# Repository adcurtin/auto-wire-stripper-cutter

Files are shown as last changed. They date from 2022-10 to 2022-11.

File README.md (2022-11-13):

# remix

this is my remix of [ProjectswithRed](https://www.youtube.com/c/ProjectswithRed)'s automatic wire stripper. I've recreated (almost) all of the 3d models with openscad, to allow for parameter tweaking. I switched the extruder to an openscad model, and tweaked that extensively as well.

# Automatic Wire Stripper and Cutter

A 3D printed automatic wire stripper and cutter. I had some old 3d printers that had been retired, I reused those parts for this project. I used a mainboard from a wanhao i3, and 24v steppers from a makerbot replicator 1 (though the wanhao steppers would've been fine at 12v). I'm using a 20V 65W lenovo laptop power supply that had a frayed end.

I'm running Marlin on this, since that can already do everything I need and I don't have to write or maintain any code :).

# Marlin notes

X and Y endstops are always triggered, so `G28` won't fail.
I modified the Z endstop to be optical, so that's inverted from the wanhao's config.

# Components

- I used some parts from old, dead 3d printers. mainboard, lcd, and rotary encode from a wanhao i3, steppers from a makerbot replicator 1, and a power supply from a lenovo laptop that had the end frayed / broken.

- [D8mm L100mm lead screw](https://www.amazon.co.uk/dp/B07QWKG317?ref_=cm_sw_r_cp_ud_dp_JMAC4EKE28W5Z3GSZSN8) (x2), for the linear motion.
- [D8mm lead screw nut](https://www.amazon.co.uk/dp/B07QWKG317?ref_=cm_sw_r_cp_ud_dp_JMAC4EKE28W5Z3GSZSN8) (x2), to attach the top blade housing to the lead screws.
- [5x8mm rigid shaft coupler](https://www.amazon.co.uk/dp/B096G1GZH5?ref_=cm_sw_r_cp_ud_dp_VWE1T2SQZQB0X13TQ1F7) (x2), to attach the lead screws to the stepper motors.
- [10mm magnets](https://www.amazon.co.uk/dp/B08FSTRRDR?ref_=cm_sw_r_cp_ud_dp_13WEC590XVADQKN2RJ0W) (x2), to attach the container.
- [KNIPEX V-blades](https://www.amazon.co.uk/dp/B00161GBDW?ref_=cm_sw_r_cp_ud_dp_S63KK1ZZ8DPRHWMBEFJC), to cut and strip the wires.

# 3D printing

Please refer to the `/3d_printing` directory.

# Assembly layout
This is the layout of the components on the board. Use this only for reference on roughly where you should fix the components to the board. I don't suggest using this for exact measurements as you should position the components where it is appropriate for your version of the project.

[Layout PDF](./assembly_layout.pdf).

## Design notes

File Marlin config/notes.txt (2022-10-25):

extruder axis - connected to original y axis - swap with E0 axis pin definition? just use e0 axis
extruder axis steps per mm - 

z axis - connected to original z axis
z axis endstop - minimum, connected to z endstop

z axis endstop sets minimum, allow jog 1mm past?
live adjust z? use this to adjust z home to be spot for stripping? or cut spot? or don't use?

z axis steps per mm - ?

lcd for melzi

shorter machine name - done

invert x and y endstops, so they're always homed, to fix homing - or just disable the endstops? and disable homing direction - done

todo:

allow Z to move past endstop a little? - how? MANUAL_[XYZ]_HOME_POS - try more - 1.6 good
longer z axis - try 90mm? try 110 then dial it back , trying 140… 135 good

check out babystepping? for live adjust z           

calibrate steps per mm on extruder          
    etrudeded 100mm, got 105mm. changed to 95mm   

more extruder speed
    try with gcode hooked up to computer
    increased manual feedrate

test running gcode from SD

NTH:

custom menu (menus?)
    check out extensible UI?

different home / status screen - custom status bitmap

bootscreen

custom predefined gcode for different lengths / wire sizes

disable x and y axes?
    no can do

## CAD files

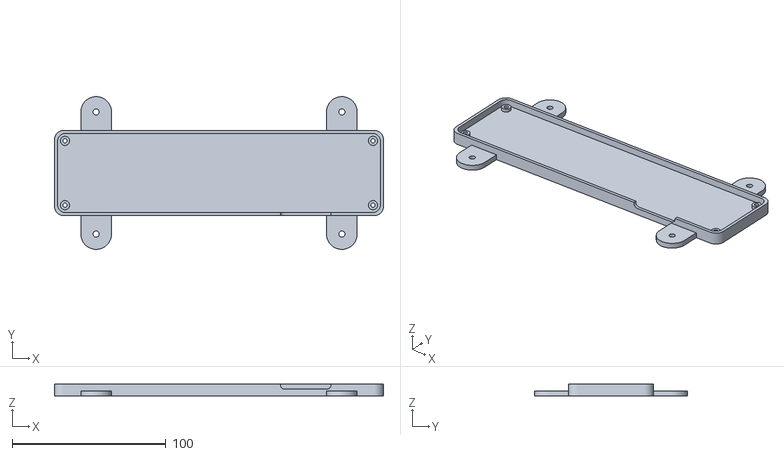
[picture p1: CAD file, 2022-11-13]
3d_printing/mainboard/mainboard case.stl
214.3 x 99.5 x 8.00

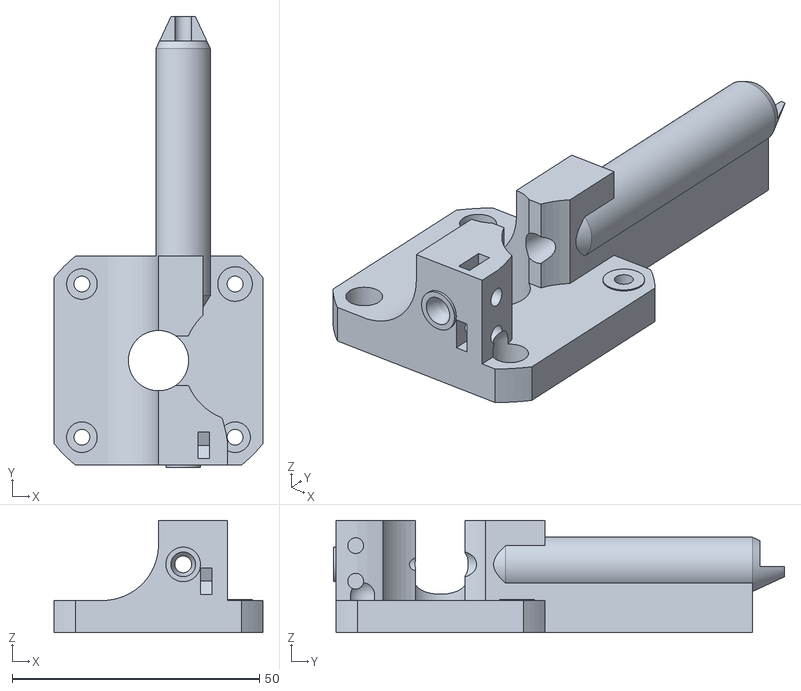
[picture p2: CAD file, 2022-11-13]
3d_printing/extruder/compact_extruder_mount motor.stl
42.3 x 91.3 x 22.7

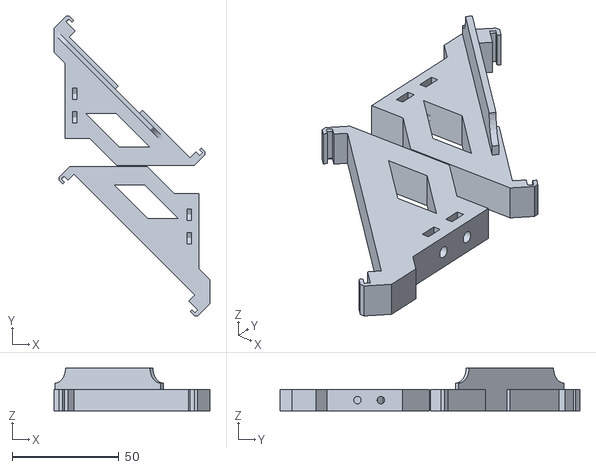
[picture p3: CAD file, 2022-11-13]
3d_printing/lcd/lcd_supports.stl
72.9 x 140.6 x 20.0

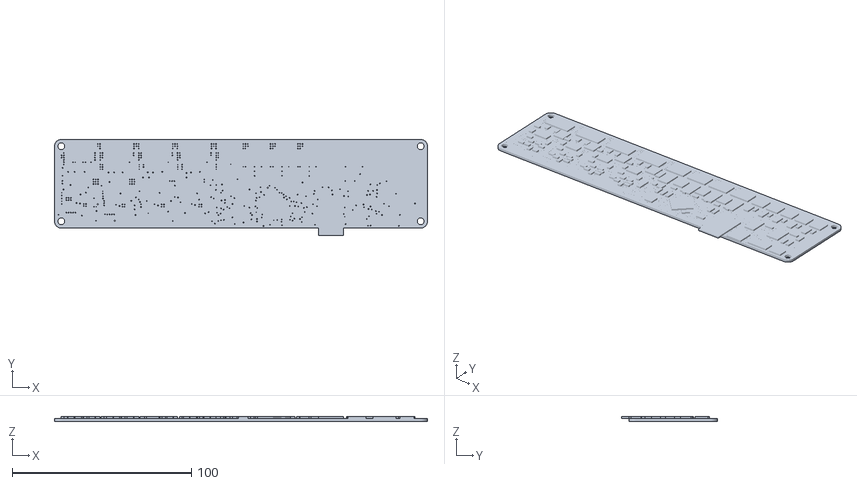
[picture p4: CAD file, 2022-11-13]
3d_printing/mainboard/melzi_pcb.stl
208.3 x 53.7 x 2.60

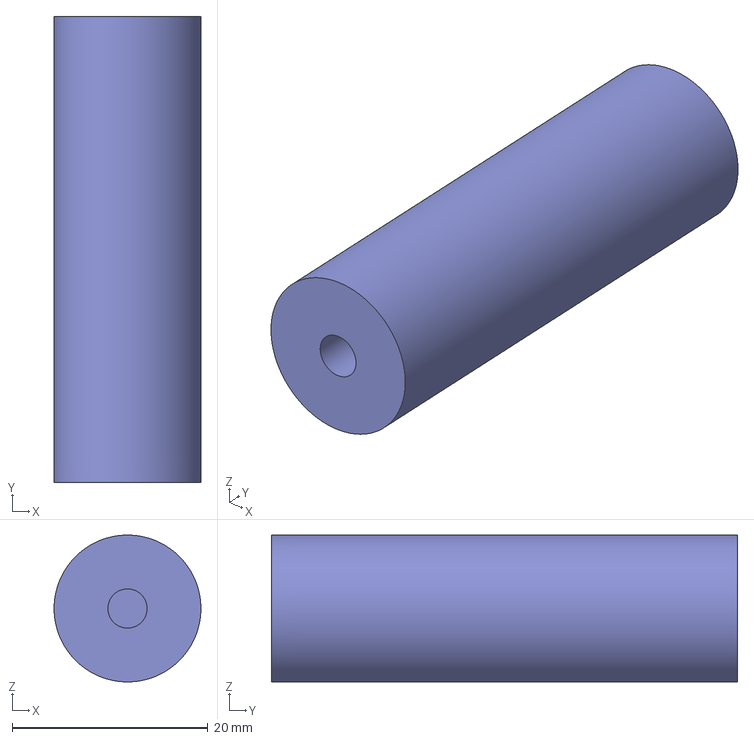
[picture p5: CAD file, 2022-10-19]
3d_printing/original models/spoolHolder_cylinder.3mf
15.0 x 47.6 x 15.0 mm

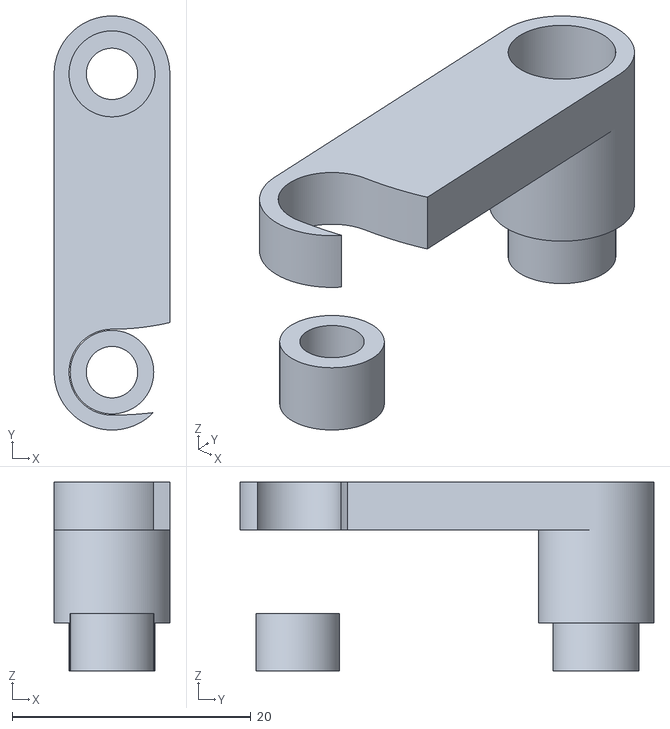
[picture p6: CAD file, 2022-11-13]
3d_printing/wire straightener/wire guide.stl
9.70 x 34.7 x 15.8

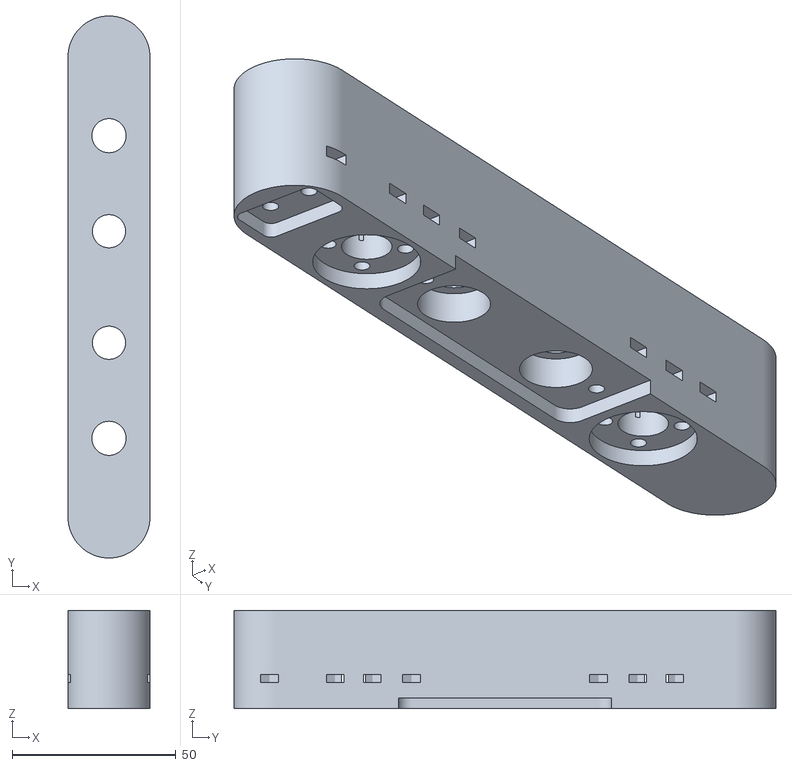
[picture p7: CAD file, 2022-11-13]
3d_printing/z axis attachment.stl
25.0 x 165.3 x 30.0

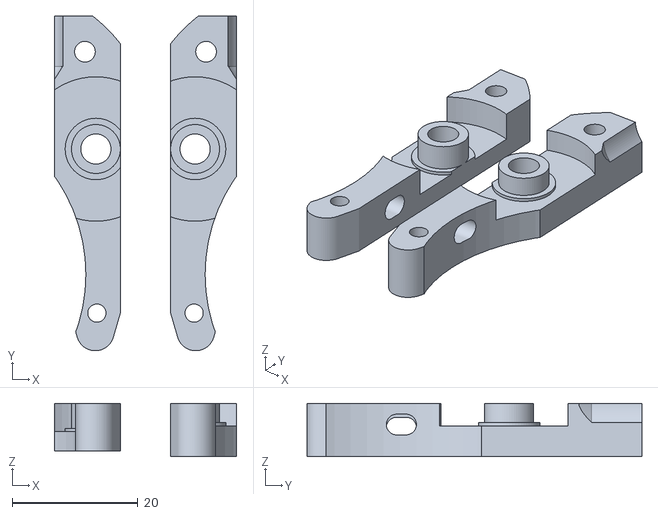
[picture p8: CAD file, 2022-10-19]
3d_printing/extruder/compact_extruder_mount idler.stl
29.0 x 53.3 x 8.45

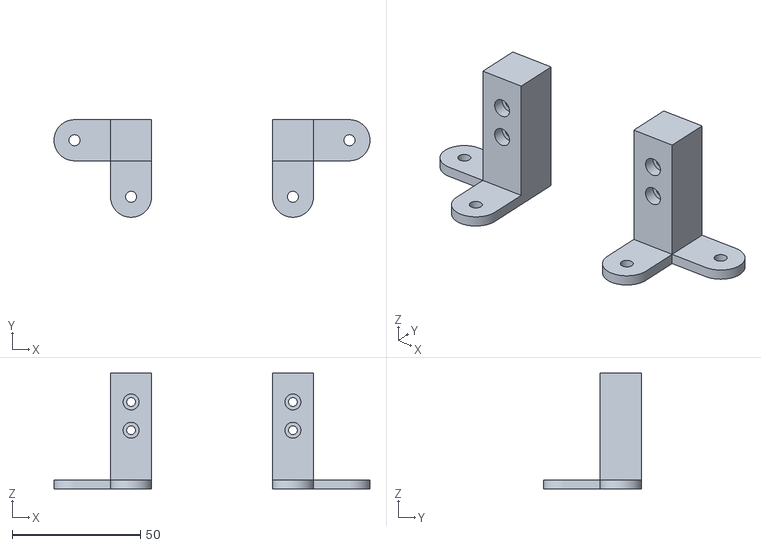
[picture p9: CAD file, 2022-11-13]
3d_printing/lcd mount.stl
123.0 x 38.0 x 45.0

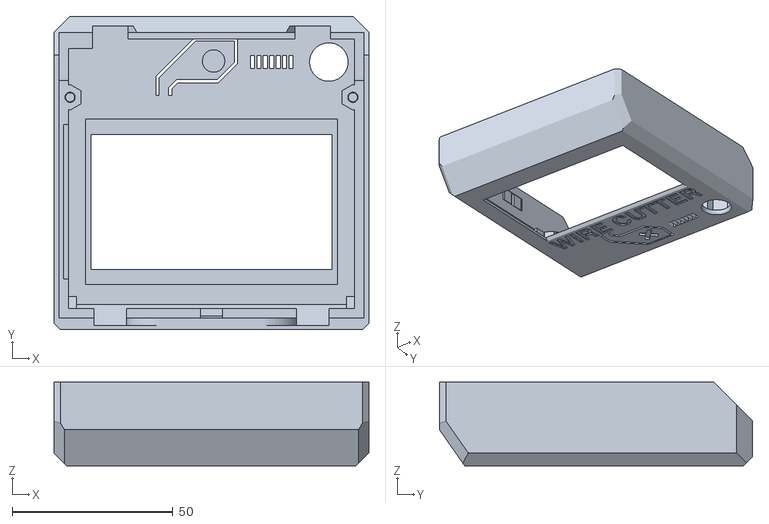
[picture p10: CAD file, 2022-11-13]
3d_printing/lcd/lcd_cover.stl
98.0 x 97.5 x 26.0

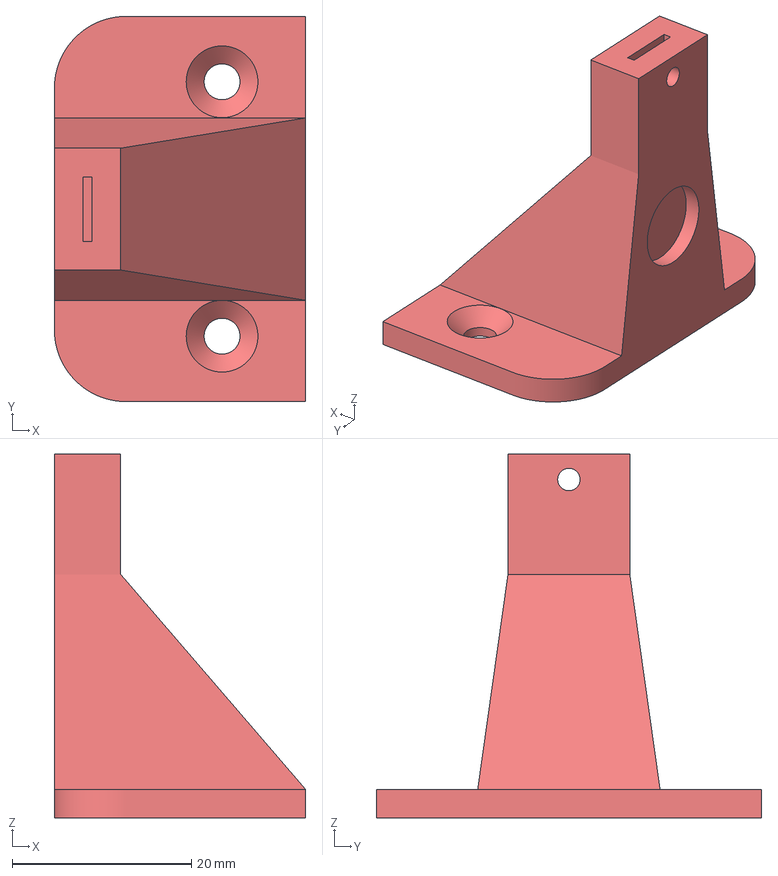
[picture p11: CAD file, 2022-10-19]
3d_printing/original models/bottomBlade_housing.3mf
28.0 x 43.0 x 40.6 mm

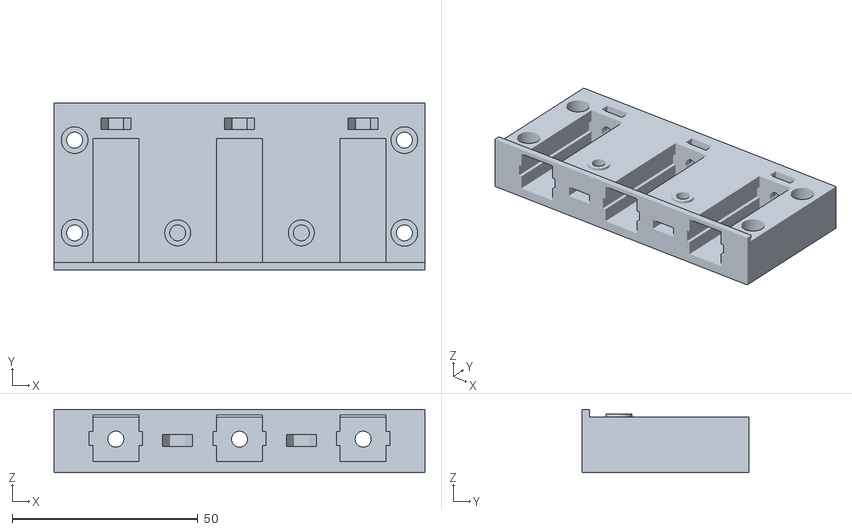
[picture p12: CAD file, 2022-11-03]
3d_printing/wire straightener/wire straightener.stl
100.0 x 45.0 x 17.0

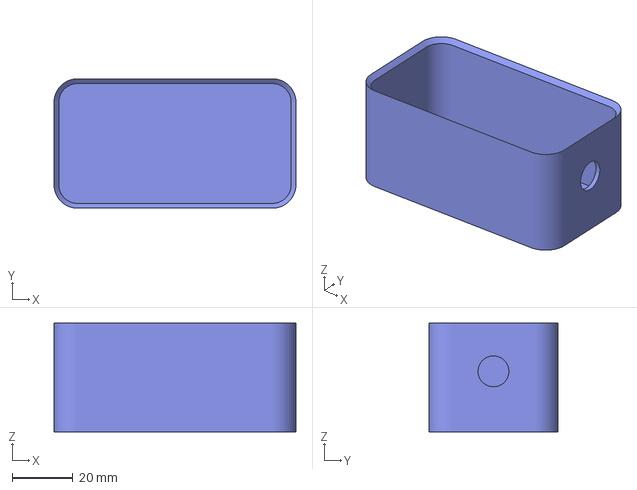
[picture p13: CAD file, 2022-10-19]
3d_printing/original models/container.3mf
80.0 x 42.8 x 36.0 mm

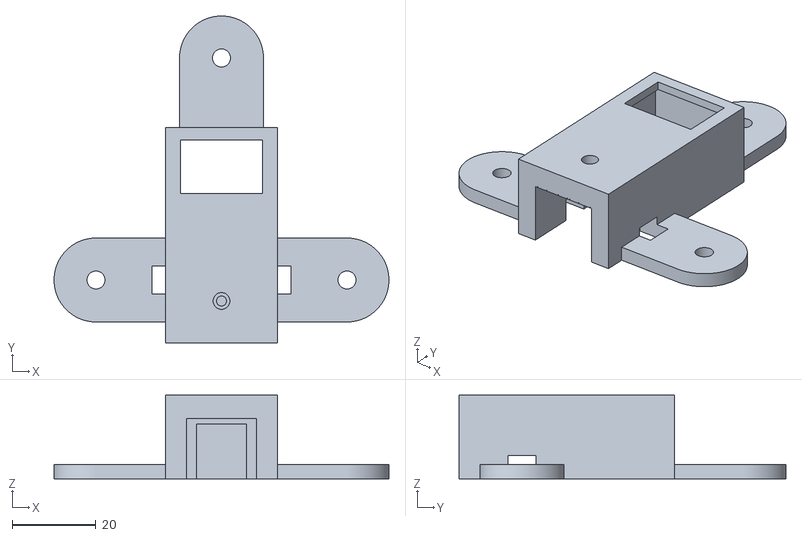
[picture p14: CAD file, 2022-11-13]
3d_printing/power module.stl
79.8 x 77.9 x 20.0

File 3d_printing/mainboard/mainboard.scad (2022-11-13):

include <OpenSCAD-common.scad>
use <melzi.scad>

// Melzi Dimensions approx 210mm x 50mm x 17mm
melzi_dimensions = [208.3, 49.55, 1.7];
melzi_hole_offset = [3.81, 3.81, 0];


$fn=50;


base_th = 3.5;

th=2;
case_clearance = 1;


case_w = melzi_dimensions[1] + 2*th + 2*case_clearance;
case_l = melzi_dimensions[0] + 2*th + 2*case_clearance;

case_h  = 8;

mount_tab_w = 20;

mount_tab_l = 35;

mount_tab_gap = 160;

mount_tab_r = 10;



// melzi_holes();/
translate([0,0,base_th + 2]) %melzi_pcb();


module mainboard_case(cutout=0){

    if(cutout==0) {
    difference() {
        translate([-case_l/2, -case_w/2, 0]) roundedRect([case_l, case_w, case_h],6);
        translate([-melzi_dimensions[0]/2 - case_clearance, -melzi_dimensions[1]/2 - case_clearance, base_th]) roundedRect([melzi_dimensions[0]+2*case_clearance, melzi_dimensions[1]+2*case_clearance, case_h],4+case_clearance);
        melzi_holes() cylinder(h=30, d=2.8, center = true);

        translate([40, -melzi_dimensions[1]/2, base_th + 1])  rotate([90, 0, 0]) roundedRect([20+13,10,10],3);
        // #translate([-100, melzi_dimensions[1]/2, th + 42])  rotate([-90, 0, 0]) roundedRect([200,40,10],7);
    }
    melzi_holes() difference() {
        cylinder(h=base_th+2, d=6);
        cylinder(h=30, d=2.8, center = true);
    }

    translate([0, 0, 0]) difference() {
        union() {
            translate([-mount_tab_w/2 + mount_tab_gap/2,  melzi_dimensions[1]/2 - mount_tab_r, 0])  roundedRect([mount_tab_w, mount_tab_l, 3.5], mount_tab_r);
            translate([-mount_tab_w/2 - mount_tab_gap/2,  melzi_dimensions[1]/2 - mount_tab_r, 0])  roundedRect([mount_tab_w, mount_tab_l, 3.5], mount_tab_r);
            translate([-mount_tab_w/2 + mount_tab_gap/2, -melzi_dimensions[1]/2 - mount_tab_l + mount_tab_r, 0])  roundedRect([mount_tab_w, mount_tab_l, 3.5], mount_tab_r);
            translate([-mount_tab_w/2 - mount_tab_gap/2, -melzi_dimensions[1]/2 - mount_tab_l + mount_tab_r, 0])  roundedRect([mount_tab_w, mount_tab_l, 3.5], mount_tab_r);
        }
        translate([ mount_tab_gap/2,  melzi_dimensions[1]/2 - 2*mount_tab_r + mount_tab_l, -1]) cylinder(h=10, d=4);
        translate([-mount_tab_gap/2,  melzi_dimensions[1]/2 - 2*mount_tab_r + mount_tab_l, -1]) cylinder(h=10, d=4);
        translate([ mount_tab_gap/2, -melzi_dimensions[1]/2 + 2*mount_tab_r - mount_tab_l, -1]) cylinder(h=10, d=4);
        translate([-mount_tab_gap/2, -melzi_dimensions[1]/2 + 2*mount_tab_r - mount_tab_l, -1]) cylinder(h=10, d=4);
    }
    }

    if(cutout) {
        translate([ mount_tab_gap/2,  melzi_dimensions[1]/2 - 2*mount_tab_r + mount_tab_l, -1]) children();
        translate([-mount_tab_gap/2,  melzi_dimensions[1]/2 - 2*mount_tab_r + mount_tab_l, -1]) children();
        translate([ mount_tab_gap/2, -melzi_dimensions[1]/2 + 2*mount_tab_r - mount_tab_l, -1]) children();
        translate([-mount_tab_gap/2, -melzi_dimensions[1]/2 + 2*mount_tab_r - mount_tab_l, -1]) children();
    
    }


}


mainboard_case(0) cylinder(h=10, d=2);

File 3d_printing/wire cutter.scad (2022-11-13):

include <OpenSCAD-common.scad>
use <extruder/compact_extruder_mount.scad>
use <wire straightener/wire straightener.scad>
use <lcd/lcd.scad>
use <mainboard/mainboard.scad>



fast_preview = 0;

module fp(){
    if(fast_preview) render() children();
    else children();
}

//animation
anim = 2*($t < 0.5 ? $t : (1-$t));

anim_height = 20*anim;

// echo(anim_height);

$fn=150;


ep = 0.01 * 1;


spool_bearing_d = 16;
spool_bearing_th = 4.9;
spool_bearing_screwhead_d = 12;
spool_bearing_screwhead_th = 3;
spool_cylinder_th = 2;
spool_cylinder_d = 18.5;
spool_h     = 48;
spool_d     = 130;


corner_rad = 7;

spool_base_x  = 40;
spool_base_y  = 53;
spool_base_th = 3.5;
spool_side_th = 4.8;


container_h = 36;
container_l = 120;
container_w = 42.8;
container_th = 2;
container_radius = 8;

container_small_l = 16;




motor_mount_th = 3.65;

nema_w = 42.3;
nema_h = 36;
nema_screw_w = 31;
nema_bushing_h = motor_mount_th;
nema_bushing_d = 23;

z_axis_stop_height = 47.5;


mech_endstop_w = 5.75;
mech_endstop_l = 12.6;
mech_endstop_h = 6.5;
mech_endstop_screw_d = 1.9;
mech_endstop_screw_gap = 6.65;
mech_endstop_screw_z_o = 1.5;


mech_endstop_e_h = 2.5; //extra height above the switch
mech_endstop_z_o =  z_axis_stop_height - mech_endstop_h - mech_endstop_e_h;//33.5 + 5;


//slop in the leadscrews, endstop springs to help

mech_endstop_spring_od = 5.3; //outside diameter for clearance
mech_endstop_spring_id = 3.4;
mech_endstop_spring_l = 25;
mech_endstop_spring_c_l = 10;

mech_endstop_spring_e_d = 5.1; //end diameter to hold the springs
mech_endstop_spring_e_l = 4;



optical_endstop_z_o = z_axis_stop_height - 8;




z_flag_base_th  = 3.25;
z_flag_base_w   = 20;
z_flag_base_l   = 12;

z_flag_base_o   = 19.65;



z_flag_w        = 2;
z_flag_l        = 8;
z_flag_h        = 10;


//z axis attachment
attachment_h = 30;
attachment_w = 25;
attachment_screw_l = 14;
attachment_nut_dp = 8;
attachment_nut_rotation = 30;

threaded_rod_d = 10.4;
blade_stepper_gap = 92.265;





//blade holder
top_blade_holder_w = 65;
top_blade_holder_r = 4;
top_blade_holder_l = 22;
top_blade_holder_h = 3.25;
top_blade_holder_screw_gap = 57;


bottom_blade_holder_w = 43;
bottom_blade_holder_r = 8;
bottom_blade_holder_l = 24.8 + 3.4;
bottom_blade_holder_h = 3.25;
bottom_blade_holder_screw_gap = 28.5;
bottom_blade_holder_screw_x = 15.4;


blade_holder_w  = 13.6;
blade_holder_l  = 8;
blade_holder_h  = 15 + .8;

//blades
blade_w = 7;
blade_th = 1;
top_blade_h = 11.25;
bottom_blade_h = 13.15;
bottom_blade_e_w = 11;
bottom_blade_e_w_h = 3.75;
bottom_blade_e_w_h_o = 2.8;

blade_cut = 3.3;
blade_notch_w = 2.5;
blade_notch_o = top_blade_h - 4.6;

blade_y_offset = 49 + blade_cut;
blade_overcut = 1;

blade_overlap = .1;
blade_over_angle = 4;


blade_holder_screw_d = 2.4;
screwhole_d = 3.3;
base_screwhole_d = 4.3;



linear_rod_d = 8.1;
linear_rod_l = 175;
linear_rod_gap = 34;

linear_bearing_d = 15;
linear_bearing_l = 17;

linear_slider_d = 15;
linear_slider_l = 40;

linear_slider_base_th = 5.3;
linear_slider_base_d = 32;
linear_slider_base_w = 21;

// linear_slider_screwhead_d = 5.6;
linear_slider_screw_d = screwhole_d;
linear_slider_screw_gap = 23.75;

linear_slider_nut_dp = 10;



mounting_board_w = 300;
mounting_board_l = 500;
mounting_board_th = 18;



module linear_slider(cutout=0) {
    difference() {
        union() {
            intersection() {
                cylinder(h=linear_slider_base_th, d=linear_slider_base_d);
                translate([-linear_slider_base_d/2, -linear_slider_base_w/2, 0]) cube([linear_slider_base_d, linear_slider_base_w, linear_slider_base_th]);
            }
            cylinder(h=linear_slider_base_th + linear_slider_l, d=linear_slider_d);
        }
        if(cutout==0) translate([0, 0, -1]) linear_rod();

        translate([linear_slider_screw_gap/2, 0, -1]) cylinder(h=linear_slider_base_th + 2, d=linear_slider_screw_d);
        translate([-linear_slider_screw_gap/2, 0, -1]) cylinder(h=linear_slider_base_th + 2, d=linear_slider_screw_d);

    }

    if(cutout) {
        translate([linear_slider_screw_gap/2, 0, -1]) cylinder(h=linear_slider_base_th + linear_slider_nut_dp + 0.5, d=linear_slider_screw_d);
        translate([-linear_slider_screw_gap/2, 0, -1]) cylinder(h=linear_slider_base_th + linear_slider_nut_dp + 0.5, d=linear_slider_screw_d);

        // nut slots
        hull() {
            translate([linear_slider_screw_gap/2, 0, linear_slider_nut_dp]) M3_hex_nut();
            translate([linear_slider_screw_gap, 0, linear_slider_nut_dp]) M3_hex_nut();
        }

        hull() {
            translate([-linear_slider_screw_gap/2, 0, linear_slider_nut_dp]) M3_hex_nut();
            translate([-linear_slider_screw_gap, 0, linear_slider_nut_dp]) M3_hex_nut();
        }
    }
}

// !linear_slider(1);


module linear_bearing() {
    difference() {
        cylinder(h=linear_bearing_l, d=linear_bearing_d);
        translate([0, 0, -1]) linear_rod();
    }
}


module linear_rod(extra_d=0) {
    cylinder(h=linear_rod_l, d=linear_rod_d + extra_d);
}



// top_blade();

module top_blade(cutout=0){
    translate([0, 0, blade_y_offset-blade_cut]) {
        if(cutout) translate([-10, 0, blade_notch_o + blade_notch_w/2]) rotate([0, 90, 0]) cylinder(h=blade_th+20, d=blade_notch_w);
        translate([0, 0, blade_cut]) rotate([0, blade_over_angle, 0]) translate([0, 0, -blade_cut]) 
        difference() {
            union() {
                translate([-blade_th, -blade_w/2, 0]) cube([blade_th, blade_w, top_blade_h]);
            }
            if(cutout==0) hull() {
                translate([-10, 0, blade_notch_o + blade_notch_w/2]) rotate([0, 90, 0]) cylinder(h=blade_th+20, d=blade_notch_w);
                translate([-1, 0, top_blade_h + blade_notch_o]) rotate([0, 90, 0]) cylinder(h=blade_th+2, d=blade_notch_w);
            }

            if(cutout==0)
            translate([0, 0, blade_cut]) 
            scale([1, 1, 1.4]) 
            rotate([180+45, 40, 0]) 
            translate([-3, 0, 0]) cube([blade_cut+4, blade_cut+1, blade_cut+1]);
        }
    }
}

module bottom_blade(cutout=0){
    translate([-blade_overlap, 0, blade_y_offset + blade_cut + blade_overcut]) rotate([0, 180, 0]) {
        if(cutout) translate([-10, 0, blade_notch_o + blade_notch_w/2]) rotate([0, 90, 0]) cylinder(h=blade_th+20, d=blade_notch_w);
        translate([0, 0, blade_cut]) rotate([0, blade_over_angle, 0]) translate([0, 0, -blade_cut])  difference() {
            union() {
                translate([-blade_th, -blade_w/2, 0]) cube([blade_th, blade_w, bottom_blade_h]);
                translate([-blade_th, -bottom_blade_e_w/2, bottom_blade_e_w_h_o]) cube([blade_th, bottom_blade_e_w, bottom_blade_e_w_h]);
            }
            if(cutout==0) hull() {
                translate([-10, 0, blade_notch_o + blade_notch_w/2]) rotate([0, 90, 0]) cylinder(h=blade_th+20, d=blade_notch_w);
                translate([-1, 0, top_blade_h + blade_notch_o]) rotate([0, 90, 0]) cylinder(h=blade_th+2, d=blade_notch_w);
            }

            if(cutout==0)
            translate([0, 0, blade_cut]) 
            scale([1, 1, 1.4]) 
            rotate([180+45, 40, 0]) 
            translate([-3, 0, 0]) cube([blade_cut+4, blade_cut+1, blade_cut+1]);
        }
    }
}

module nema17(screw_len = 15, cutout=0){
    translate([-nema_w/2, -nema_w/2, 0]) cube([nema_w, nema_w, nema_h]);
    translate([nema_screw_w/2, nema_screw_w/2, nema_h]) cylinder(h=screw_len, d=screwhole_d);
    translate([-nema_screw_w/2, nema_screw_w/2, nema_h]) cylinder(h=screw_len, d=screwhole_d);
    translate([nema_screw_w/2, -nema_screw_w/2, nema_h]) cylinder(h=screw_len, d=screwhole_d);
    translate([-nema_screw_w/2, -nema_screw_w/2, nema_h]) cylinder(h=screw_len, d=screwhole_d);

    hull() {
        translate([0, 0, nema_h - 0.01]) cylinder(h=nema_bushing_h +2, d=nema_bushing_d);
        if(cutout) {
            translate([0, 0, nema_h - 0.01]) cylinder(h=nema_bushing_h +10 +z_axis_stop_height, d=nema_bushing_d);
            translate([nema_w, 0, nema_h - 0.01]) cylinder(h=nema_bushing_h +10 +z_axis_stop_height, d=nema_bushing_d);
        }
    }

    //stepper shaft
    translate([0, 0, nema_h]) cylinder(h=15, d=5);
}

module mech_endstop_switch(screw_len = 0){
    difference() {
        translate([-mech_endstop_l/2, 0, 0]) cube([mech_endstop_l, mech_endstop_w, mech_endstop_h]);

        translate([mech_endstop_screw_gap/2, -1, mech_endstop_screw_z_o]) rotate([270,0,0]) cylinder(h=2*mech_endstop_w, d= mech_endstop_screw_d);
        translate([-mech_endstop_screw_gap/2, -1, mech_endstop_screw_z_o]) rotate([270,0,0]) cylinder(h=2*mech_endstop_w, d= mech_endstop_screw_d);
    }
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

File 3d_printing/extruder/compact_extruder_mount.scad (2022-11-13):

// Avoid openscad artefacts in preview
use <OpenSCAD-common.scad>
epsilon = 0.01 * 1;

$fn=100;

// Which one would you like to see?
part = "both"; // [first:Main Part,second:Idler,both:Main Part and Idler]




// Select idler version (V2 should provide further strength, but is bulkier)
idler_version = 2; // [1:V1 (open design), 2:V2 (closed two part splitted design)]

idler_bushing_d = 7;
idler_bushing_h = 0.2;

idler_screw_len = 16;
idler_screwhead_d = 11;

// Increase this if your slicer or printer make holes too tight (default 0.1)
extra_radius = 0.1;

// Add a clamping handle (manually remove tension for filament insertion)
add_clamping_handle = 1; // [0:No, 1:Yes]

// Add a M3 screwhole trough handle (only for V2 idler) - use a M3 screw and corresonding nut to add further strength
add_handle_screw = 1;  // [0:No, 1:Yes]

tensioner_bolt_gap = 4;

// Major diameter of metric 3mm thread
m3_major = 2.85*1;
m3_radius = 3.2/2;//m3_major / 2 + extra_radius; //for m3 clearance holes
m3_wide_radius = 3.3/2;//m3_major / 2 + extra_radius + 0.2;

// echo(2*m3_radius);

// Diameter of metric 3mm hexnut screw head
m3_head_radius = 3 + extra_radius;

// Height of base (default: 5mm)
base_height = 5*1 + 1.5;        // [2:0.1:10]

/* [Drive gear parameters] */
// Outer diameter of drive gear
drive_gear_dia = 9;
drive_gear_outer_radius = drive_gear_dia / 2;

// Diameter of hobbed section
drive_gear_hobbed_dia = 7.4;
drive_gear_hobbed_radius = drive_gear_hobbed_dia / 2;

// How far is the hobbed section away from outer face
drive_gear_hobbed_offset = 3.2;

// Height of drive gear (only important for gears with height >13mm)
drive_gear_height = 11;
drive_gear_length = max(13, drive_gear_height);
drive_gear_tooth_depth = 0.2;


/* [Mounting Options] */
add_mounting_plate = 0; // [0:None,1:Anet A8 Mount,2: Generic Mount]

// Base width for frame plate (Generic mount only)
base_width = 15;
// Base width for frame plate (Generic mount only)
base_length = 60;


top_height = 1*4.9;




// Stepper (nema 17) dimensions
nema17_width = 42.3 * 1;
nema17_hole_offsets = [
	[-15.5, -15.5, 2.5],
	[-15.5,  15.5, 2.5],
	[ 15.5, -15.5, 2.5],
	[ 15.5,  15.5, 1.5 + base_height]
];



/* [Filament Inlet] */

// Select inlet type (For now: normal and M5 pushfit without thread as option!)
inlet_type = 0; // [0:Normal, 1:Pushfit]


/* [Filament Outlet] */
// Add thread to hole (set to 'no', if your printer can't handle fine details)
outlet_thread = 0; // [0:No, 1:Yes]

// Select your pushfit thread (recommended: M5)
outlet_dia = 8; // [5:M5, 6:M6, 7:M7, 8:M8, 9:M9, 10:M10]


//length of the outlet guide tube
outlet_len = 42 + 6.5 - 1;
//output
outlet_base_len = 42;
outlet_tip_len = 6.5;


/* [Filament Diameter] */
// Choose your filament diameter
filament_diameter = 3; // [1.75:1.75, 3.00:3.00]
filament_offset = [
	drive_gear_hobbed_radius + filament_diameter / 2 - drive_gear_tooth_depth,
	0,
	base_height + drive_gear_length - drive_gear_hobbed_offset - 2.5
];




// helper function to render a rounded slot
module rounded_slot(r = 1, h = 1, l = 0, center = false)
{
	hull()
	{
		translate([0, -l / 2, 0])
			cylinder(r = r, h = h, center = center);
		translate([0, l / 2, 0])
			cylinder(r = r, h = h, center = center);
	}
}


// mounting plate for nema 17
module nema17_mount()
{
	// settings
	width = nema17_width;
	height = base_height;
	edge_radius = 27;
	axle_radius = drive_gear_outer_radius + 1 + extra_radius;

	difference()
	{
		// base plate
		translate([0, 0, height / 2])
            union() {
    			intersection()
    			{
    				cube([width, width, height], center = true);
    				cylinder(r = edge_radius, h = height + 2 * epsilon, $fn = 128, center = true);
    			}
                translate([nema17_hole_offsets[3][0], nema17_hole_offsets[3][1], base_height/2]) cylinder(h=idler_bushing_h, d=idler_bushing_d);
            }

        // translate([filament_diameter + 1 + filament_offset[0], -nema17_width / 2 + 4, base_height])
        // hull() {
        //     rotate([0, 90, 0]) cylinder(r = 3.15 + 2.5 * extra_radius - .1, h = 2.5 + 3 * extra_radius, center = true, $fn = 6);
        //     translate([0, 0, -20]) rotate([0, 90, 0]) cylinder(r = 3.15 + 2.5 * extra_radius - .1, h = 2.5 + 3 * extra_radius, center = true, $fn = 6);
        
        // }

		// center hole
		translate([0, 0, -epsilon]	)
			cylinder(r = 6 + extra_radius, h = base_height + 2 * epsilon, $fn = 64);

		// axle hole
		translate([0, 0, -epsilon])
			cylinder(r = axle_radius, h = height + 2 * epsilon, $fn = 64);

		// mounting holes
		for (a = nema17_hole_offsets)
			translate(a)
			{
				cylinder(r = m3_radius, h = height * 4, center = true, $fn = 50);
				cylinder(r = m3_head_radius, h = height + epsilon, $fn = 50);
			}

	}
}


// plate for mounting extruder on frame
module frame_mount()
{
	// settings
	width = base_width;
	length = base_length;
	height = base_height;
	hole_offsets = [
		[0,  length / 2 - 6, 2.5],
		[0, -length / 2 + 6, 2.5]
	];
	corner_radius = 3;

	difference()
	{
		// base plate
		intersection()
		{
			union()
			{
				translate([0, 0, height / 2])
					cube([width, length, height], center = true);
				translate([base_width / 2 - base_height / 2 - corner_radius / 2, 0, height + corner_radius / 2])
					cube([base_height + corner_radius, nema17_width, corner_radius], center = true);
				translate([base_width / 2 - base_height / 2, 0, 6])
					cube([base_height, nema17_width, 12], center = true);
			}

			cylinder(r = base_length / 2, h = 50, $fn = 64);
		}

		// rounded corner
		translate([base_width / 2 - base_height - corner_radius, 0, height + corner_radius])
			rotate([90, 0, 0])
				cylinder(r = corner_radius, h = nema17_width + 2 * epsilon, center = true, $fn = 64);

		// mounting holes
		for (a = hole_offsets)
			translate(a)
			{
				cylinder(r = m3_wide_radius, h = height * 2 + 2 * epsilon, center = true, $fn = 50);
				cylinder(r = m3_head_radius, h = height + epsilon, $fn = 50);
			}

		// nema17 mounting holes
		translate([base_width / 2, 0, nema17_width / 2 + base_height])
			rotate([0, -90, 0])
			for (a = nema17_hole_offsets)
				translate(a)
				{
					cylinder(r = m3_radius, h = height * 4, center = true, $fn = 50);
					cylinder(r = m3_head_radius, h = height + epsilon, $fn = 50);
				}
	}
}

// plate for mounting extruder on frame
module frame_mount_anet()
{
    base_width_anet = 15;
    base_length_anet = 60;

	// settings
	width = 60;
	length = nema17_width+base_height;
	height = base_height;
	hole_offsets = [
		[40,  length / 2 - 8, 2.5],
		[40-23, length / 2 - 8 - 16, 2.5]
	];
	corner_radius = 3;

	difference()
	{
		// base plate
        union(){
            intersection()
            {
                union()
                {
                    translate([20, -height / 2, height / 2])
                        cube([width, length, height], center = true);
                    translate([base_width_anet / 2 - base_height / 2 - corner_radius / 2, -height / 2, height + corner_radius / 2])
                        cube([base_height + corner_radius, nema17_width+height, corner_radius], center = true);
                    translate([base_width_anet / 2 - base_height / 2, -height / 2, 6])
                        cube([base_height, nema17_width+height, 12], center = true);
                }

                union(){
                    translate([25, -height / 2, 0])
                    cylinder(r = base_length_anet / 2, h = 50, $fn = 64);
                    translate([15, -height / 2, 0])
                    cylinder(r = base_length_anet / 2, h = 50, $fn = 64);
                }
            }
            // Triangle support

            difference(){
                translate([height/2+2*epsilon, -length/2 - height/2 + epsilon, epsilon])
                    cube([40,height , 36]);

                translate([0, -length/2 - height/2 - 2*epsilon, 43.5])
                    rotate([0,45,0])
                        cube([60,height + 4*epsilon, 30]);
            }
        }

		// rounded corner
		translate([base_width_anet / 2 - base_height - corner_radius, -height / 2, height + corner_radius])
			rotate([90, 0, 0])
				cylinder(r = corner_radius, h = nema17_width + height + 2 * epsilon, center = true, $fn = 64);

		// mounting holes
		for (a = hole_offsets)
			translate(a)
			{
				cylinder(r = m3_wide_radius, h = height * 2 + 2 * epsilon, center = true, $fn = 50);
				cylinder(r = m3_head_radius, h = height + epsilon, $fn = 50);
			}

		// nema17 mounting holes
		translate([base_width_anet / 2, 0, nema17_width / 2 + base_height])
			rotate([0, -90, 0])
			for (a = nema17_hole_offsets)
				translate(a)
				{
					cylinder(r = m3_radius, h = height * 4, center = true, $fn = 50);
					cylinder(r = m3_head_radius, h = height + epsilon, $fn = 50);
				}
	}
}


// inlet for filament
module filament_tunnel()
{
	// settings
	width = 8;
	length = nema17_width;
	height = filament_offset[2] - base_height + 4;
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

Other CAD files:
3d_printing/wire straightener/wire straightener slider.stl
3d_printing/original models/wire_channel.3mf
3d_printing/wire straightener mount.stl
3d_printing/endstop mount.stl
3d_printing/lcd/lcd.scad
3d_printing/bottom blade holder.stl
3d_printing/container.stl
3d_printing/container_small.stl
3d_printing/endstop mount reverse.stl
3d_printing/lcd/lcd_cover.scad
3d_printing/lcd/lcd_supports.scad
3d_printing/mainboard/melzi.scad
3d_printing/original models/linearMotion_attachment.3mf
3d_printing/original models/spoolHolder_base.3mf
3d_printing/original models/spoolHolder_cylinder_cap.3mf
3d_printing/original models/topBlade_housing.3mf
3d_printing/original models/wiring_housing.3mf
3d_printing/original models/wiring_housing_lid.3mf
3d_printing/power module insert.stl
3d_printing/spool holder cylinder long.stl
3d_printing/spool_holder.stl
3d_printing/spool_holder_cap.stl
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

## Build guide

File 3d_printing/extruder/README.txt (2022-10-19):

Customizable Bowden Extruder | Mount for ANET A8 & Others by TNS on Thingiverse: https://www.thingiverse.com/thing:2204941

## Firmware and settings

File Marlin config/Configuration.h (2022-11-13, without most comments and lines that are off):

#pragma once
#define CONFIGURATION_H_VERSION 02010200
#define STRING_CONFIG_H_AUTHOR "(adcurtin)" // Who made the changes.
#define SHOW_BOOTSCREEN
#define SHOW_CUSTOM_BOOTSCREEN
  #define MOTHERBOARD BOARD_MELZI
#define SERIAL_PORT 0
#define BAUDRATE 250000
#define CUSTOM_MACHINE_NAME "Wire Stripper"
#define X_DRIVER_TYPE  A4988
#define Y_DRIVER_TYPE  A4988
#define Z_DRIVER_TYPE  A4988
#define E0_DRIVER_TYPE A4988
#define EXTRUDERS 1
#define DEFAULT_NOMINAL_FILAMENT_DIA 1.75
#define TEMP_SENSOR_0 999
#define TEMP_SENSOR_1 0
#define TEMP_SENSOR_2 0
#define TEMP_SENSOR_3 0
#define TEMP_SENSOR_4 0
#define TEMP_SENSOR_5 0
#define TEMP_SENSOR_6 0
#define TEMP_SENSOR_7 0
#define TEMP_SENSOR_BED 0
#define TEMP_SENSOR_PROBE 0
#define TEMP_SENSOR_CHAMBER 0
#define TEMP_SENSOR_COOLER 0
#define TEMP_SENSOR_BOARD 0
#define TEMP_SENSOR_REDUNDANT 0
#define DUMMY_THERMISTOR_998_VALUE  25
#define DUMMY_THERMISTOR_999_VALUE 100
#if TEMP_SENSOR_IS_MAX_TC(0)
  #define MAX31865_SENSOR_OHMS_0      100 // (Ω) Typically 100 or 1000 (PT100 or PT1000)
  #define MAX31865_CALIBRATION_OHMS_0 430 // (Ω) Typically 430 for Adafruit PT100; 4300 for Adafruit PT1000
#endif
#if TEMP_SENSOR_IS_MAX_TC(1)
  #define MAX31865_SENSOR_OHMS_1      100
  #define MAX31865_CALIBRATION_OHMS_1 430
#endif
#if HAS_E_TEMP_SENSOR
  #define TEMP_RESIDENCY_TIME         10  // (seconds) Time to wait for hotend to "settle" in M109
  #define TEMP_WINDOW                  1  // (°C) Temperature proximity for the "temperature reached" timer
  #define TEMP_HYSTERESIS              3  // (°C) Temperature proximity considered "close enough" to the target
#endif
#if TEMP_SENSOR_BED
  #define TEMP_BED_RESIDENCY_TIME     10  // (seconds) Time to wait for bed to "settle" in M190
  #define TEMP_BED_WINDOW              1  // (°C) Temperature proximity for the "temperature reached" timer
  #define TEMP_BED_HYSTERESIS          3  // (°C) Temperature proximity considered "close enough" to the target
#endif
#if TEMP_SENSOR_CHAMBER
  #define TEMP_CHAMBER_RESIDENCY_TIME 10  // (seconds) Time to wait for chamber to "settle" in M191
  #define TEMP_CHAMBER_WINDOW          1  // (°C) Temperature proximity for the "temperature reached" timer
  #define TEMP_CHAMBER_HYSTERESIS      3  // (°C) Temperature proximity considered "close enough" to the target
#endif
#if TEMP_SENSOR_REDUNDANT
  #define TEMP_SENSOR_REDUNDANT_SOURCE    E1  // The sensor that will provide the redundant reading.
  #define TEMP_SENSOR_REDUNDANT_TARGET    E0  // The sensor that we are providing a redundant reading for.
  #define TEMP_SENSOR_REDUNDANT_MAX_DIFF  10  // (°C) Temperature difference that will trigger a print abort.
#endif
#define HEATER_0_MINTEMP   5
#define HEATER_1_MINTEMP   5
#define HEATER_2_MINTEMP   5
#define HEATER_3_MINTEMP   5
#define HEATER_4_MINTEMP   5
#define HEATER_5_MINTEMP   5
#define HEATER_6_MINTEMP   5
#define HEATER_7_MINTEMP   5
#define BED_MINTEMP        5
#define CHAMBER_MINTEMP    5
#define HEATER_0_MAXTEMP 260
#define HEATER_1_MAXTEMP 260
#define HEATER_2_MAXTEMP 260
#define HEATER_3_MAXTEMP 260
#define HEATER_4_MAXTEMP 260
#define HEATER_5_MAXTEMP 260
#define HEATER_6_MAXTEMP 260
#define HEATER_7_MAXTEMP 260
#define BED_MAXTEMP      120
#define CHAMBER_MAXTEMP  60
#define HOTEND_OVERSHOOT 15   // (°C) Forbid temperatures over MAXTEMP - OVERSHOOT
#define BED_OVERSHOOT    10   // (°C) Forbid temperatures over MAXTEMP - OVERSHOOT
#define COOLER_OVERSHOOT  2   // (°C) Forbid temperatures closer than OVERSHOOT
#define PIDTEMP          // See the PID Tuning Guide at https://reprap.org/wiki/PID_Tuning
#define BANG_MAX 255     // Limits current to nozzle while in bang-bang mode; 255=full current
#define PID_MAX BANG_MAX // Limits current to nozzle while PID is active (see PID_FUNCTIONAL_RANGE below); 255=full current
#define PID_K1 0.95      // Smoothing factor within any PID loop
    #define DEFAULT_Kp  29.0
    #define DEFAULT_Ki   2.0
    #define DEFAULT_Kd  97.0
#define MAX_BED_POWER 255 // limits duty cycle to bed; 255=full current
#define MAX_CHAMBER_POWER 255 // limits duty cycle to chamber heater; 255=full current
  #define PID_FUNCTIONAL_RANGE 10 // If the temperature difference between the target temperature and the actual temperature
#define PREVENT_LENGTHY_EXTRUDE
#define EXTRUDE_MAXLENGTH 200
#define USE_XMIN_PLUG
#define USE_YMIN_PLUG
#define USE_ZMIN_PLUG
#define ENDSTOPPULLUPS
#define X_MIN_ENDSTOP_INVERTING false  // Set to true to invert the logic of the endstop.
#define Y_MIN_ENDSTOP_INVERTING false  // Set to true to invert the logic of the endstop.
#define Z_MIN_ENDSTOP_INVERTING false  // Set to true to invert the logic of the endstop.
#define I_MIN_ENDSTOP_INVERTING false // Set to true to invert the logic of the endstop.
#define J_MIN_ENDSTOP_INVERTING false // Set to true to invert the logic of the endstop.
#define K_MIN_ENDSTOP_INVERTING false // Set to true to invert the logic of the endstop.
#define U_MIN_ENDSTOP_INVERTING false // Set to true to invert the logic of the endstop.
#define V_MIN_ENDSTOP_INVERTING false // Set to true to invert the logic of the endstop.
#define W_MIN_ENDSTOP_INVERTING false // Set to true to invert the logic of the endstop.
#define X_MAX_ENDSTOP_INVERTING false // Set to true to invert the logic of the endstop.
#define Y_MAX_ENDSTOP_INVERTING false // Set to true to invert the logic of the endstop.
#define Z_MAX_ENDSTOP_INVERTING false // Set to true to invert the logic of the endstop.
#define I_MAX_ENDSTOP_INVERTING false // Set to true to invert the logic of the endstop.
#define J_MAX_ENDSTOP_INVERTING false // Set to true to invert the logic of the endstop.
#define K_MAX_ENDSTOP_INVERTING false // Set to true to invert the logic of the endstop.
#define U_MAX_ENDSTOP_INVERTING false // Set to true to invert the logic of the endstop.
#define V_MAX_ENDSTOP_INVERTING false // Set to true to invert the logic of the endstop.
#define W_MAX_ENDSTOP_INVERTING false // Set to true to invert the logic of the endstop.
#define Z_MIN_PROBE_ENDSTOP_INVERTING false // Set to true to invert the logic of the probe.
#define DEFAULT_AXIS_STEPS_PER_UNIT   { 80, 80, 400, 90 }
#define DEFAULT_MAX_FEEDRATE          { 700, 700, 200, 10000 }
#define DEFAULT_MAX_ACCELERATION      { 3000, 3000, 100, 10000 }
#define DEFAULT_ACCELERATION                   700  // X, Y, Z ... and E acceleration for printing moves
#define DEFAULT_RETRACT_ACCELERATION          3000  // E acceleration for retracts
#define DEFAULT_TRAVEL_ACCELERATION            700  // X, Y, Z ... acceleration for travel (non printing) moves
#define DEFAULT_EJERK    5.0  // May be used by Linear Advance
  #define JUNCTION_DEVIATION_MM 0.02  // (mm) Distance from real junction edge
  #define JD_HANDLE_SMALL_SEGMENTS    // Use curvature estimation instead of just the junction angle
#define NOZZLE_TO_PROBE_OFFSET { 10, 10, 0 }
#define PROBING_MARGIN 10
#define XY_PROBE_FEEDRATE (133*60)
#define Z_PROBE_FEEDRATE_FAST (4*60)
#define Z_PROBE_FEEDRATE_SLOW (Z_PROBE_FEEDRATE_FAST / 2)
#define Z_CLEARANCE_DEPLOY_PROBE   10 // Z Clearance for Deploy/Stow
#define Z_CLEARANCE_BETWEEN_PROBES  5 // Z Clearance between probe points
#define Z_CLEARANCE_MULTI_PROBE     5 // Z Clearance between multiple probes
#define Z_PROBE_LOW_POINT          -2 // Farthest distance below the trigger-point to go before stopping
#define Z_PROBE_OFFSET_RANGE_MIN -20
#define Z_PROBE_OFFSET_RANGE_MAX 20
#define X_ENABLE_ON 0
#define Y_ENABLE_ON 0
#define Z_ENABLE_ON 0
#define E_ENABLE_ON 0 // For all extruders
#define DISABLE_X false
#define DISABLE_Y false
#define DISABLE_Z false
#define DISABLE_E false             // Disable the extruder when not stepping
#define DISABLE_INACTIVE_EXTRUDER   // Keep only the active extruder enabled
#define INVERT_X_DIR false
#define INVERT_Y_DIR false
#define INVERT_Z_DIR true
#define INVERT_E0_DIR true
#define INVERT_E1_DIR false
#define INVERT_E2_DIR false
#define INVERT_E3_DIR false
#define INVERT_E4_DIR false
#define INVERT_E5_DIR false
#define INVERT_E6_DIR false
#define INVERT_E7_DIR false
#define Z_AFTER_HOMING  5      // (mm) Height to move to after homing Z
#define X_HOME_DIR -1
#define Y_HOME_DIR -1
#define Z_HOME_DIR -1
#define X_BED_SIZE 200
#define Y_BED_SIZE 200
#define X_MIN_POS 0
#define Y_MIN_POS 0
#define Z_MIN_POS -8
#define X_MAX_POS X_BED_SIZE
#define Y_MAX_POS Y_BED_SIZE
#define Z_MAX_POS 135
#define MIN_SOFTWARE_ENDSTOPS
  #define MIN_SOFTWARE_ENDSTOP_X
  #define MIN_SOFTWARE_ENDSTOP_Y
  #define MIN_SOFTWARE_ENDSTOP_Z
  #define MIN_SOFTWARE_ENDSTOP_I
  #define MIN_SOFTWARE_ENDSTOP_J
  #define MIN_SOFTWARE_ENDSTOP_K
  #define MIN_SOFTWARE_ENDSTOP_U
  #define MIN_SOFTWARE_ENDSTOP_V
  #define MIN_SOFTWARE_ENDSTOP_W
#define MAX_SOFTWARE_ENDSTOPS
  #define MAX_SOFTWARE_ENDSTOP_X
  #define MAX_SOFTWARE_ENDSTOP_Y
  #define MAX_SOFTWARE_ENDSTOP_Z
  #define MAX_SOFTWARE_ENDSTOP_I
  #define MAX_SOFTWARE_ENDSTOP_J
  #define MAX_SOFTWARE_ENDSTOP_K
  #define MAX_SOFTWARE_ENDSTOP_U
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

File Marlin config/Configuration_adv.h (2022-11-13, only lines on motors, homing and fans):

#define E0_AUTO_FAN_PIN -1
#define E1_AUTO_FAN_PIN -1
#define E2_AUTO_FAN_PIN -1
#define E3_AUTO_FAN_PIN -1
#define E4_AUTO_FAN_PIN -1
#define E5_AUTO_FAN_PIN -1
#define E6_AUTO_FAN_PIN -1
#define E7_AUTO_FAN_PIN -1
#define CHAMBER_AUTO_FAN_PIN -1
#define COOLER_AUTO_FAN_PIN -1
#define HOMING_BUMP_MM      { 5, 5, 2 }       // (linear=mm, rotational=°) Backoff from endstops after first bump
#define HOMING_BUMP_DIVISOR { 2, 2, 4 }       // Re-Bump Speed Divisor (Divides the Homing Feedrate)
#define MICROSTEP_MODES { 16, 16, 16, 16, 16, 16 } // [1,2,4,8,16]
  #define BABYSTEP_WITHOUT_HOMING

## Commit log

2022-10-19 first commit. it works! y motor gets too hot though, and lots still to test
    [bottomBlade_housing.3mf, compact_extruder_mount combined.stl, compact_extruder_mount idler.stl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]
2022-10-25 added preliminary Marlin configuration and tweaked blade holders and endstop mount
    added preliminary Marlin configuration to use the marlin firmware.
    redesigned blade holders for better height alignment and blade holding
    added endstop mount to detect end bottom of z travel. added springs to help with the play in the leadscrew nuts so the blade will properly clear when closing. proabbly need to add some smooth rods to keep it more rigid.
    [Configuration.h, Configuration_adv.h, bottom blade holder.stl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]
2022-10-31 added linear rods, commit before changing the blade holders
    [compact_extruder_mount.scad, container.stl, wire cutter.scad]
2022-11-03 linear rails
    added linear rails for precise alignment. machine is able to remove insulation from one end of 26awg wire
    [Configuration.h, Configuration_adv.h, bottom blade holder.stl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]
2022-11-13 version 1.0
    it works well now, seems to be fairly consistent. considering this a version 1.0.
    switched to an optical endstop. added LCD, mainboard, and power module models.
    [Configuration.h, Configuration_adv.h, compact_extruder_mount motor.stl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]
2022-11-29 wrapping up this project for now. adding more gcode for some other wire sizes

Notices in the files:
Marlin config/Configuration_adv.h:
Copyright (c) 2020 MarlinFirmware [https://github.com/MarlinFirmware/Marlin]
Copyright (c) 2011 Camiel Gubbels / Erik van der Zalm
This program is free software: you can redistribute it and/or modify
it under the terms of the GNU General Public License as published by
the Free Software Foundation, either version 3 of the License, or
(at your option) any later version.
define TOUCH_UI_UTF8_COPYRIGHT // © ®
